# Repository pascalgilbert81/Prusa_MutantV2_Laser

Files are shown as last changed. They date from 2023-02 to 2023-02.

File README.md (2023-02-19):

# Prusa MK3S+ MUTANT V2 [laser cutter](https://youtu.be/tXEEcxm7fwQ) mod

## Introduction
Check out the video linked in the title. After going through these instructions
that's what you should end up with.

A Prusa MK3S+ printer has been upgraded with the Whambam Mutant V2 system. The
mod was done following mediaman's instructions:
[Prusa MUTANT Upgrade Kit](https://www.thingiverse.com/thing:4948925)

### Additional notes when going for the Z-height extension
Here a few things to consider when following the instructions
- you do not need the two parts
  - `z-axis-top-M_left.stl`
  - `z-axis-top-M_right.stl`
- instead print the `Optional-X-end-idler-M-tall.stl` part
- no need for these parts
  - `MK2.5S_x-endstop-left-M.stl`
  - `fan-shroud.stl`
  - `adapter-printer.stl`
  - `x-endstop-right-M.stl`
  - `extruder-cover.stl`
- as the name suggests, you need two copies of `y-rod-holder-M_x2`
  - for people suffering from the same condition as myself, mirror one part, though not strictly necessary
- when building the x-carriage, add some sort of screw on the righthand side, which allows to adjust the X-endstop. it should bump into the z-carriage assembly at around 255mm from home
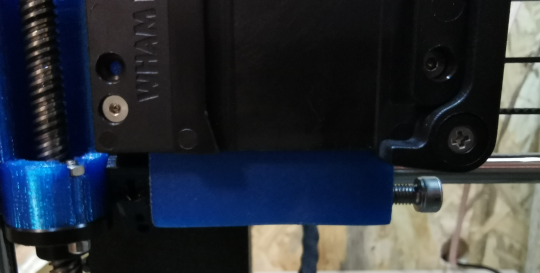
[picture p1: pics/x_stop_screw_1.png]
X Stop Screw

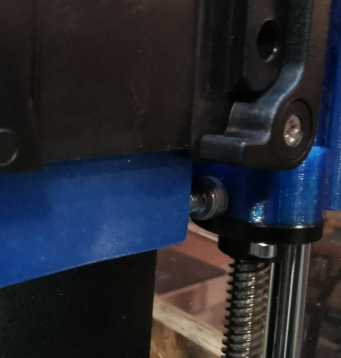
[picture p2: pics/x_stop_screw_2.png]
X Stop bumped to the right


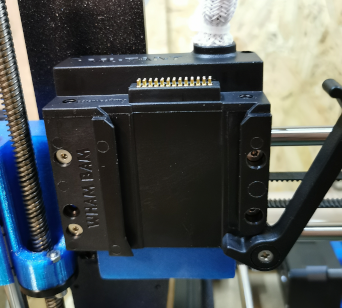
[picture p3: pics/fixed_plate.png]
fixed plate


The original Prusa E3D v6 hotend can now easily be re-built using the parts provided by
the mediaman.

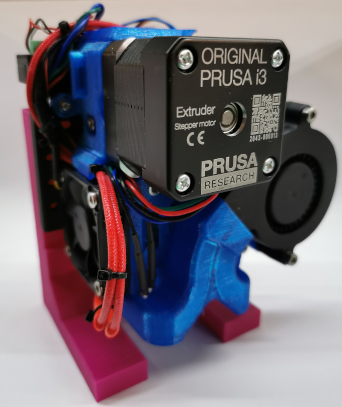
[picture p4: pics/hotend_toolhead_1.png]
original hotend

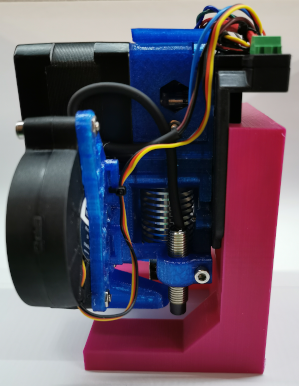
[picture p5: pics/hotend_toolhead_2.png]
original hotend

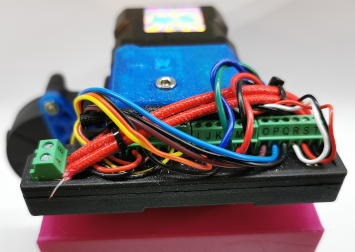
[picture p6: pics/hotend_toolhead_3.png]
original hotend


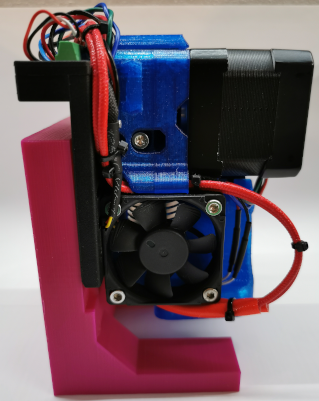
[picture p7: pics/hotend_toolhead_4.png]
original hotend

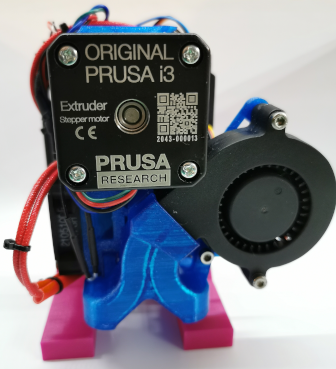
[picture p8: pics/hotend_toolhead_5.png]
original hotend


## Wiring diagram fixed plate
The following pinout is used for the fixed plate. It follows closely the reference
pinout provided by Whambam.

| Pin | Signal Name | uC I/O | max I |
|-----|---|---|---|
| A | Hotend 24V | PWR | 10A |
| B | Hotend GND | open drain | 10A |
| C | Thermistor + | ADC in | 3A |
| D | Thermistor - | PWR | 3A |
| E | Hotend Fan 5V | PWR | 3A |
| F | Hotend Fan GND | open drain | 3A |
| G | Hotend Fan TACH | IN | 3A |
| H | Parts Fan TACH | IN | 3A |
| I | Parts Fan 5V | PWR | 3A |
| J | Parts Fan GND | open drain | 3A |
| K | Motor E blue | DRV out | 3A |
| L | Motor E green | DRV out | 3A |
| M | Motor E red | DRV out | 3A |
| N | Motor E black | DRV out | 3A |
| O | PINDA 5V (brown) | PWR | 3A |
| P | PINDA GND (blue) | PWR | 3A |
| Q | PINDA sig (black)  | IN | 3A |
| R | Filament sense sig | IN | 3A |
| S | Filament Sense 5V  | PWR | 3A |
| T | Filament sense GND | PWR | 3A |
| | | | |

## The Laser

### Disclaimer
Lasers can be extremely dangerous and lead to blindness. Obviously all modifications
are at your own risk and should only be done by well educated people and only
while wearing appropriate eye protection. Note the wavelength and optical power
of your specific laser when purchasing the protective googles.

### Mechanical mounting
Mounting the laser to the mobile plate is as easy as driving a couple of screws
from the back through the mobile plate into the threaded holes of the laser.
It is recommended to use a minimum of two screws, better three or more for a secure
fixation of the laser module.

### Electrical connections
When shopping for the laser module, make sure it is a 24V variant, as this is the
hotend voltage on the Prusa MK3S+ printer. For other printers a 12V laser might
be more suitable. In order to keep the firmware modifications to a minimum, the
hotend temperature is simulated to be constant around 52°C by connecting a 30.1K ohm
resistor to the thermistor terminals. You may also use a spare thermistor which would
measure room temperature. Finally it is also possible to use a potentiometer of 100K
total resistance, which allows to set the temperature to some value of your liking.

Furthermore, the permanent 24V power output is used to feed the laser module. As
the GND return path, any ground wire can be used. To modulate the Laser power
the parts fan PWM output is used. Some electronics is required to make the open-drain
output suitable as a logic level signal for most lasers expecting a PWM signal
between 0 and 5V. You may need to adjust the schematics if your particular laser
module expects some other type of signal (analog, different logic high voltage, ...)

Refer to the following schematic using two pull-up resistors of 470ohm and one
N-channel MOSFET to invert the signal polarity.

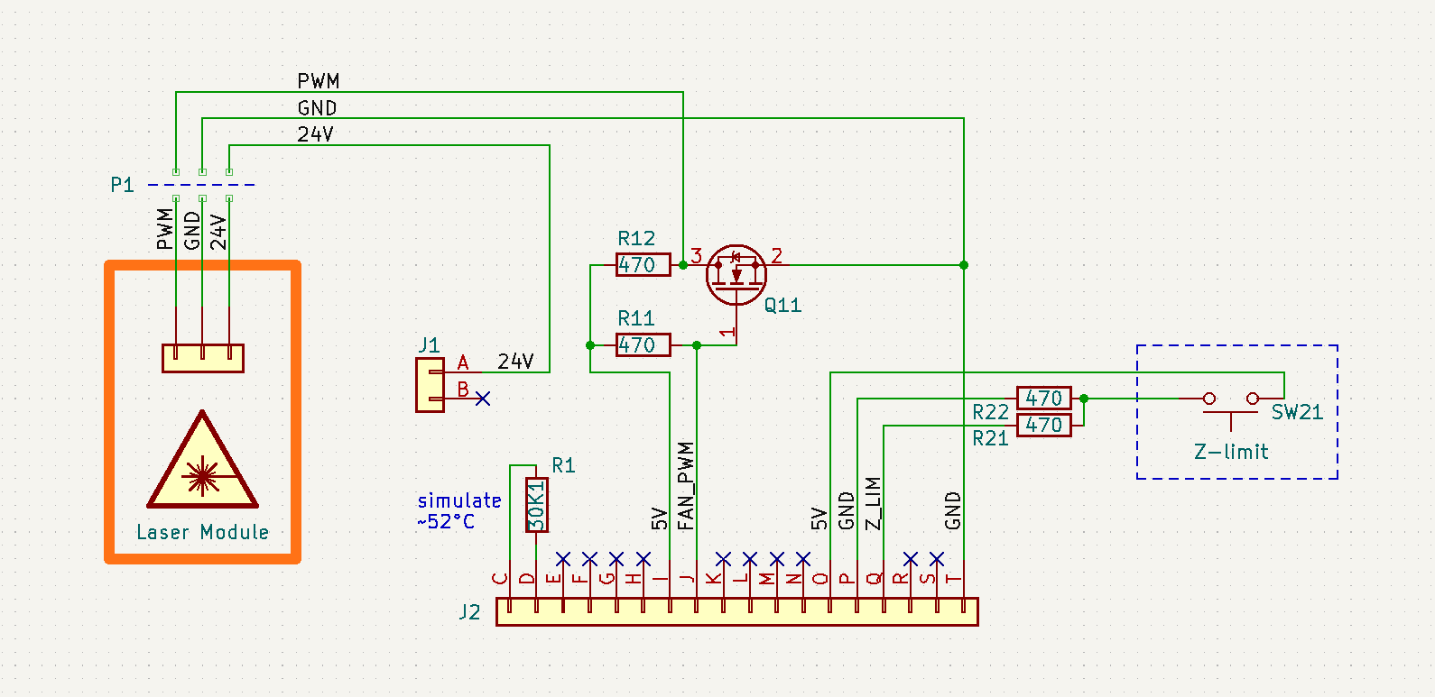
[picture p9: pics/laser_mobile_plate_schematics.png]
Schematic


#### wiring of laser
| Pin | Signal Name |
|-----|---|
| A | LASER 24V+ |
| B | |
| C | 30K1 ohm to C |
| D | 30K1 ohm from D |
| E | |
| F | |
| G | |
| H | |
| I | 5V for pull-up |
| J | LASER PWM control  |
| K | |
| L | |
| M | |
| N | |
| O | 5V for Z-limit SW  |
| P | GND for Z-limit SW |
| Q | Z-limit SW |
| R | |
| S | |
| T | LASER GND |
| | |

### additional Z-height limit switch
At this point your laser mod should be ready for use. It is necessary to set the
Z-height manually using the Prusa's user interface before starting a lasercut/engraving
job. Make sure to interrupt the power to the laser while you are homing the head
and adjusting the height. Note that you will have to add a PINDA probe for Z-homing
to work.

A better way than fixing a PINDA probe to the mobile plate and having to adjust
the optimal cutting height before every cut is to add a momentary switch, which
can detect the surface of the work piece at the beginning of every job. Refer to
the following simple schematic on how to use a simple normally open momentary
microswitch to replace the PINDA probe. To fix the switch to the mobile plate,
some 3D printing might be required.

Once the switch is in place, make sure it can touch the surface before any sort
of air-assist nozzle would ram into the build-plate. The switch should also be off
the surface by a couple of millimeters when the optimal focal distance is set.

Follow this procedure to determine the perfect focal length:
 1. home the printer `Calibrate -> Auto home`
 2. manually move the Z-axis up until the perfect distance between the surface and
the laser body is reached. to do this in small steps, it is necessary to connect
Pronterface to the Prusa, as the firmware only allows to move in steps of 1 mm
 3. note the absolute Z-distance either by reading it off of the LCD, or by issuing
the M114 command in Pronterface
 4. adjust the header script with the determined Z-height.

Refer to [this video](https://youtu.be/BLlMHWbL5m0) for a walkthrough on how to
do it using Pronterface.

### Prusa firmware
Finally a small firmware modification is required for the Laser to work properly.
This sounds scarier than it is. A branch with the modifications can be found
[here](https://github.com/pascalgilbert81/Prusa-Firmware-MutantV2/tree/modify/mutant_z_height)
Note that this mod also includes a higher max Z height necessary for the initial
calibration to run successfully. The firmware can be downloaded and compiled according
to the original instructions provided in the README, the mod has only been done for the
*1_75mm_MK3S-EINSy10a-E3Dv6full* variant. An already compiled and tested version
can be downloaded from [here](https://github.com/pascalgilbert81/Prusa-Firmware-MutantV2/releases/tag/MutantV2_Laser). Using this binary is entirely at your own risk, for that reason it is highly
recommended that you compile the firmware yourself.

#### Why a custom firmware?
The firmware will not do a fan check when booting and will not try to determine what type
of fan is used as the parts cooler. This is necessary, as there is no tacho signal
coming from the printer because there is no fan installed. Furthermore the PWM signal controlling
the parts cooling fan is used to set the Laser power.

### Pictures
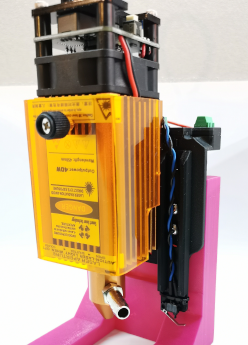
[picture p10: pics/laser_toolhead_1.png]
laser toolhead

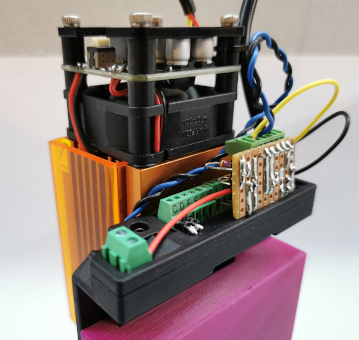
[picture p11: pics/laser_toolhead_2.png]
laser toolhead

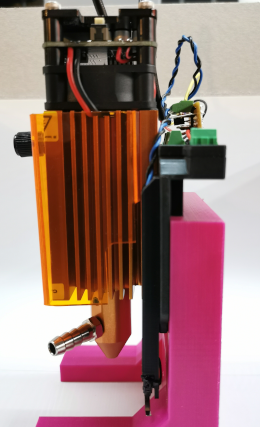
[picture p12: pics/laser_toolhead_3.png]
laser toolhead


### Generating gcode for the laser
There is a number of ways how to generate gcode for lasercutting/engraving. One simple
and free, yet limited way is to use inkscape with a specialized plugin. It will
convert any paths to gcode instructions. Download and install the
[J-Tech-Photonics-Laser-Tool](https://github.com/JTechPhotonics/J-Tech-Photonics-Laser-Tool)
according to their instructions.

#### customize settings and generate gcode
1. set cutting speed, output directory and filename to suit your project (these settings need to be adjusted according to the job at hand)
2. define the Tool Power Command and Tool Off Command
3. point to the custom g-code header/footer files, download from [here](gcode)
4. hit apply and you'll be presented with your first gcode file, provided that you did draw something on the canvas and convert it to a path (refer to the official J-Tech instructions).

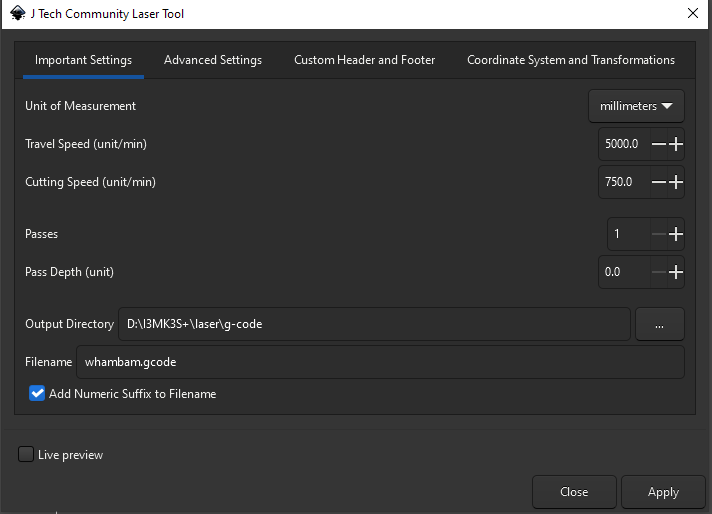
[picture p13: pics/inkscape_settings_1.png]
inkscape plugin settings


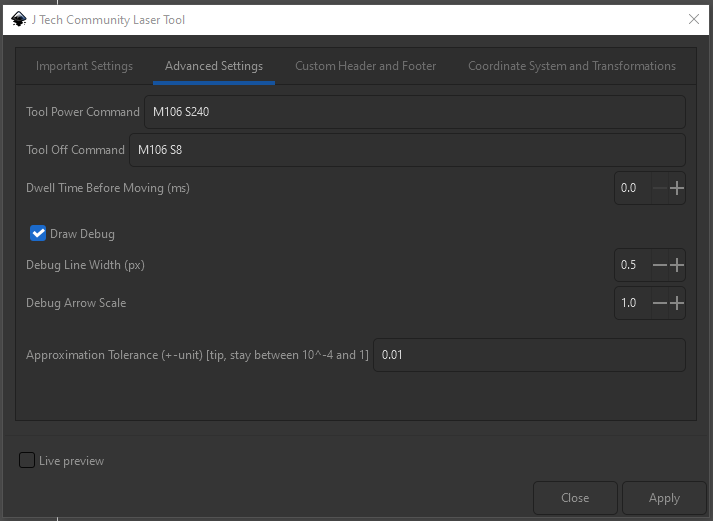
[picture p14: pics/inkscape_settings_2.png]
inkscape plugin settings


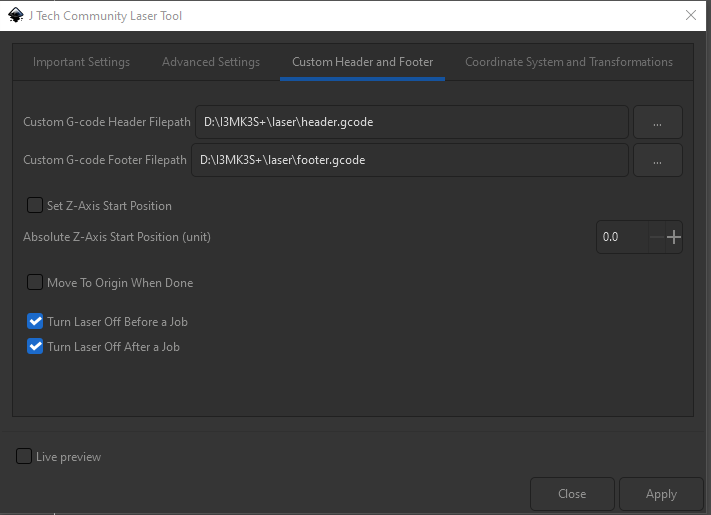
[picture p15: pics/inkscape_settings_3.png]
inkscape plugin settings


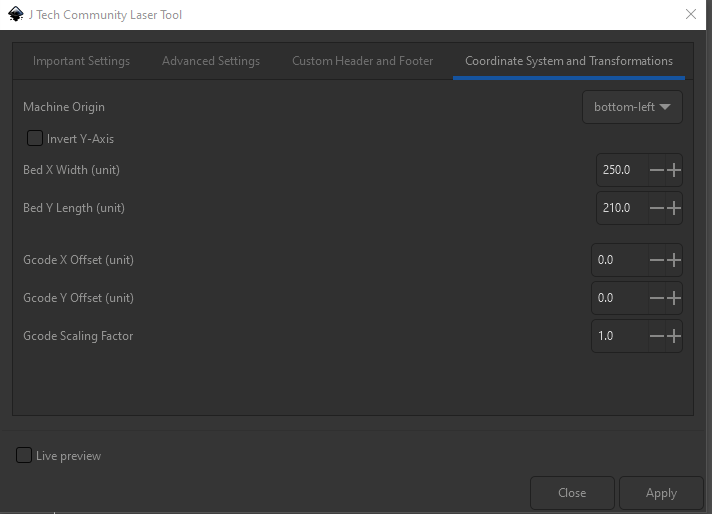
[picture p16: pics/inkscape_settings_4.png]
inkscape plugin settings


## Conclusion

Enjoy!

Feel free to leave feedback, open issues on this git repo to help me improve these instructions

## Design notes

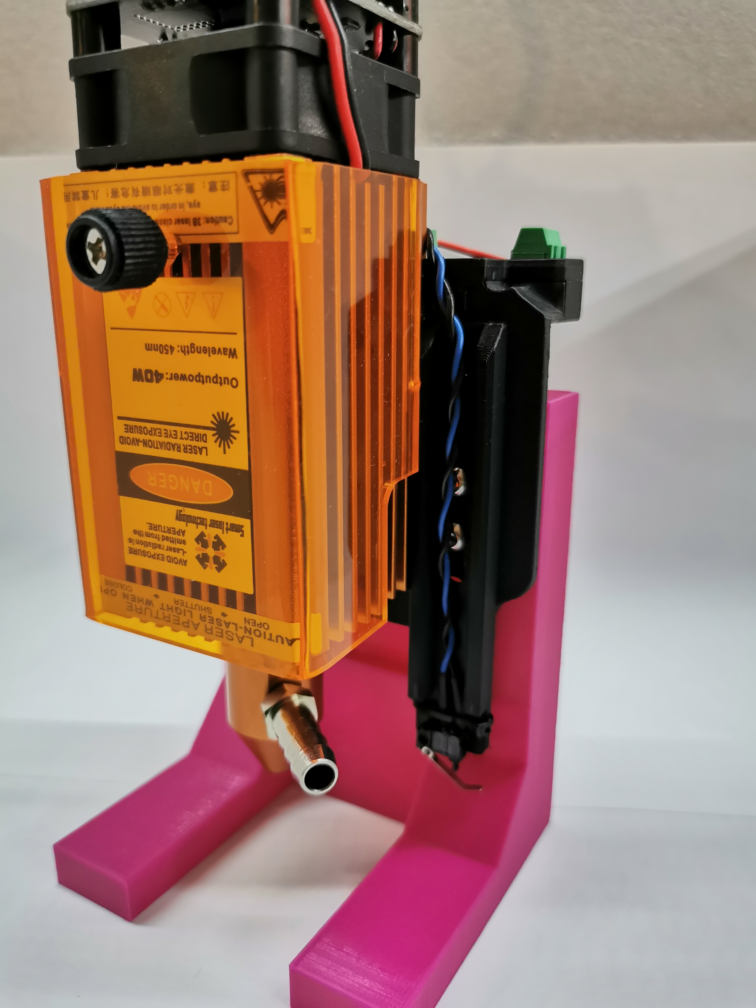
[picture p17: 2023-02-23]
pics/high_res/5Woptical_laser.jpg

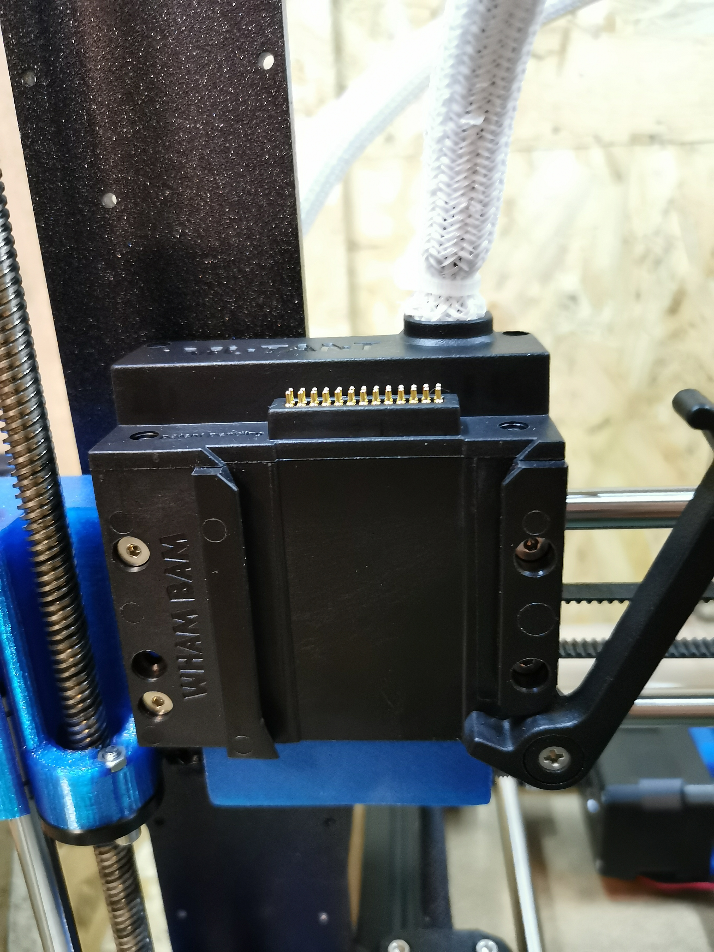
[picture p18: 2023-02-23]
pics/high_res/fixed_plate.jpg

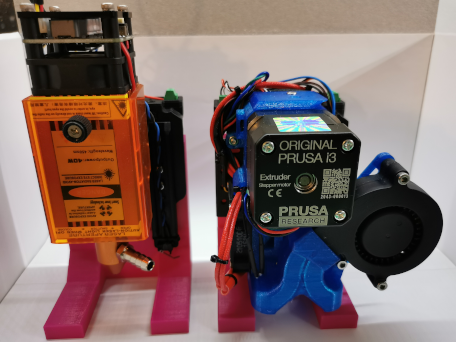
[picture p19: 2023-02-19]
pics/toolheads.png

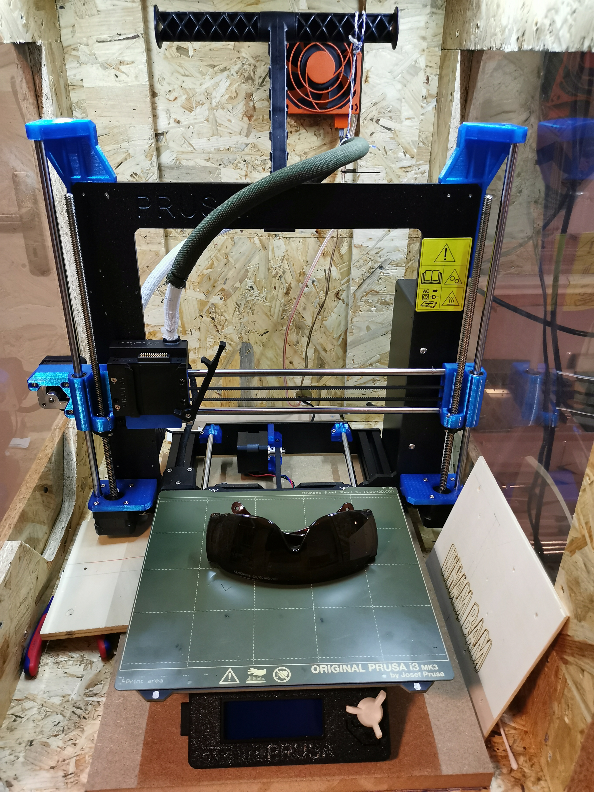
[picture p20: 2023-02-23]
pics/high_res/prusa_mk3splus_mutant_v2.jpg

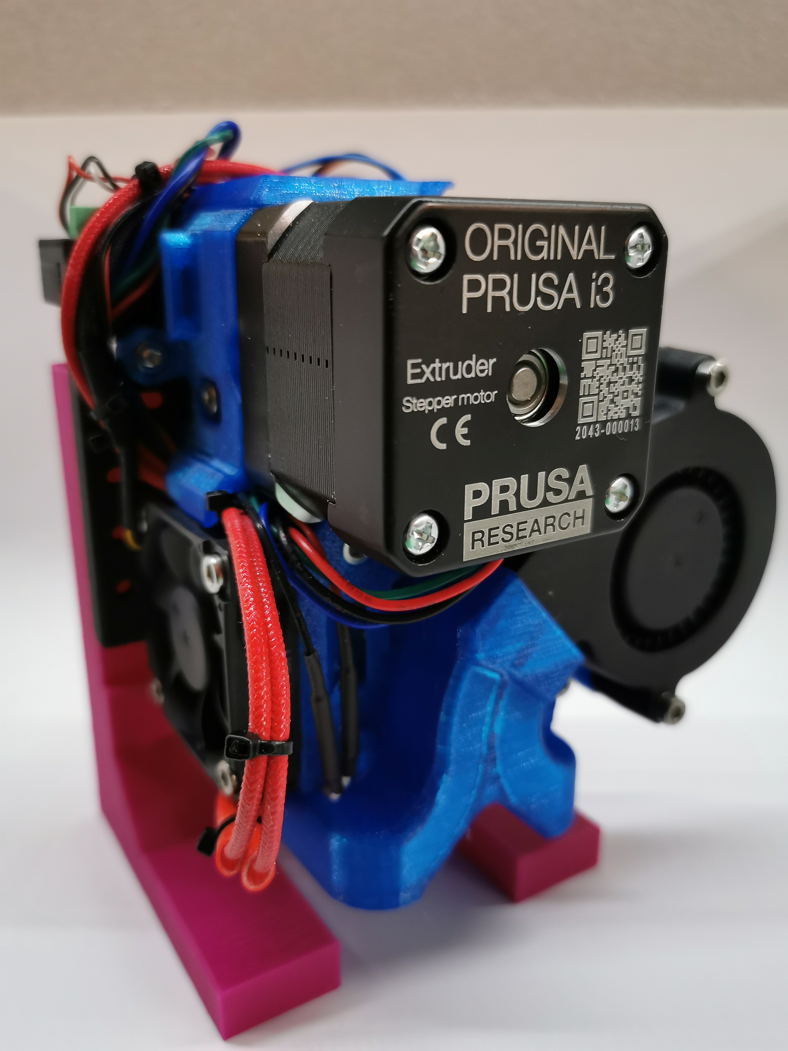
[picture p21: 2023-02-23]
pics/high_res/prusa_hotend.jpg
